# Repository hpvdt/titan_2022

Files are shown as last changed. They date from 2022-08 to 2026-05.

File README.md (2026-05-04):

# TITAN Video System

This is the code and hardware that is used to drive the electronics aboard TITAN for the "drive-by-video" system used for the World Human Powered Speed Challenge 2022.

>[!NOTE]
> This repository is meant to a snapshot of the system used for the 2022 system for TITAN, and was archived in November 2023. It was only unarchived to add a written summary of [operating instructions](./OPERATION.md) should it need to be reused. However no changes to the system itself have happened since 2023.
>
> For information on the the newest system in 2026 please go to that one's [separate repository](https://github.com/savob/titan_2026).

This code is spread across two types of devices, an STM32 microcontroller (STM32F103C8 is used in current models) and Raspberry Pis (RPi) Model 3B+'s. Each rider has an RPi for a total of two units, while there is only one STM32 for the vehicle. The STM32 is primarily responsible for collecting vehicle data and passing it to the RPis when requested. The RPis are responsible for displaying the video feed from the RPi Cameras used (hence why each rider needs their own) with an overlay of data collected inside the vehicle. This overlay is tailored to each rider.

There is an additional redundant video system for the front rider based on analog video to minimize potential failure points. This system was entirely off the shelf except for the power regulator, and was entirely disconnected from the remainder of TITAN's electronics to prevent any failure cascade affecting it.

## Folders

The repository is split into folders based on function.

Folder | Purpose
------ | -------
`Hardware` | Hardware files for our circuit boards
`Microcontroller Code` | STM32 Code
`vision` | RPi video code in C

## Hardware

The hardware for TITAN was all designed in [KiCad](https://www.kicad.org/) there are all three boards designed for TITAN with a `readme.md` explaining their purposes. Below is a block diagram of the TITAN system.

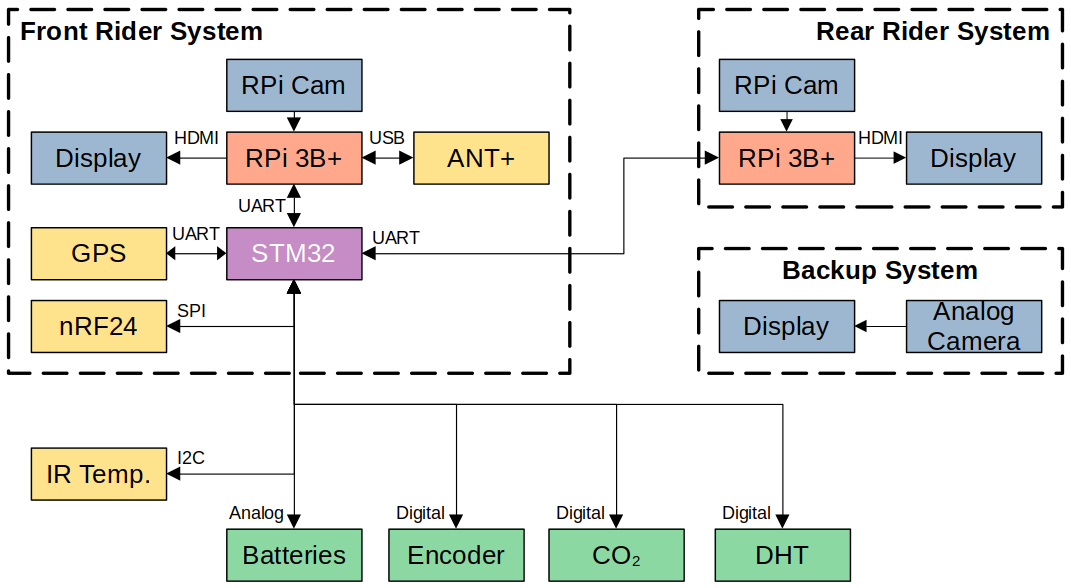
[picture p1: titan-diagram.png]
TITAN Block Diagram


## Microcontroller Code

This is the collection of code prepared for the microcontroller on TITAN. It contains the unit tests we prepared when developing and testing different features that would eventually be integrated into TITAN, a local copy of the GPS library we use, and the overall program for TITAN.

TITAN was initially coded entirely within the Arduino IDE, however we migrated to using VS Code and PlatformIO to help make development easier and also make use of debugging features absent in the original Arduino IDE.

## Raspberry Pi Code

These are responsible for putting video on the displays for the riders to see, overlaid with information about TITAN. One of the RPi's has an ANT+ USB module used to collect data from the heart rate monitor and power pedals each rider has and feed it to the STM32 to pass onto the other RPi.

**The program for running the video feed is run as a separate process to the overlay**, this way if there is a hardware malfunction for the overlay (e.g. the STM32 freezes) then the video feed is uninterrupted for the riders.

The code for vision is split between Python and C. The video related code is written in Python, as well as a few other scripts for operation. The overlay code is written in C using the chipset driver library unique to the RPi 3 hardware to draw the overlay so it cannot be used on RPi models other then the 3B or 3B+ (and must be compiled specifically for each model).

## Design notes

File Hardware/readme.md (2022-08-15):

# TITAN Hardware

These folders contain the files related to hardware designed to operate TITAN. They were all designed using KiCad 6.0.2.

## Overview

The TITAN hardware is designed to primarily be a HAT (**HA**rdware on **T**op) for the Raspberry Pi 3B+s we use for video. This form factor was chosen to reduce the overall footprint of the system compared to the original 2019 system which used a ribbon cable between the RPi and boards. This also reduces the chance of incorrect connections since the HAT can only be seated one way. At the heart of the HAT, there is an STM32F103C microcontroller which communicates with the RPis and various sensors around TITAN via the various connections present.

These HATs perform 4 main functions:
1. Regulate power for their RPi and monitor from the battery. (Reverse polarity and undervoltage protection built in).
2. Facilitate communication between RPis via an STM32 microcontroller
3. Collect data from TITAN using the STM32 microcontroller
4. Handle telemetry with the chase vechicle

**Functions 2 to 4 are only performed on the "main" (front) unit, where the STM32 is.** The secondary (rear) does not have the STM32 mounted and just uses the power system and a header to connect to the main board for data.

## The Boards

There are three boards/folders/projects present in the folder, representing two revisions of the hardware. 

### TITAN Redux (2020)

Following feedback from the 2019 WHPSC and experience in developing [Blueshift](https://github.com/hpvdt/blueshift), an initial revision of TITAN was made in the fall of 2020, dubbed `titan_redux`. This was the main revision from the 2019 system, moving to the HAT form factor which worked on Blueshift as well as moving to embed the microconroller directly on the board (as opposed to seating a "Blue Pill" development board) and using SMT to reduce the overall size.

This was largely successful and allowed most of the code that went into TITAN in 2022 to be properly tested. There were only two notable issues with it:
1. The RX and TX lines for the GPS were not properly crossed over to the STM32.
2. The 5V regulator was removed for undocumented reasons, likely due to a failure.

### TITAN 2022

The more straightforwardly named `titan_2022` is a revision of the Redux board. It addresses the issues it had as well as adding support for new features while maintaining the same RPi HAT form. A brief of the changes:

- Fixed UART lines
- Rearranged board for improved button access
- Rearranged sensors to simplify routing
- Changed to a different 5V regulator (largely due to supply issues)
- Moved DHT sensor and encoder comparator off-board
- Added headers for monitoring CO2 and brake temperature

### TITAN Wheel (2022)

As part of the revision process from redux to the 2022 system a daughter board to collect wheel data was prepared called `titan_wheel`. This board houses the brake temperature sensor as well as the optical encoder and its conditioning circuitry. It was designed to fit within the wheel structure close to the brake disk.

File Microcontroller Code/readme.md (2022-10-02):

# Microcontroller Code

There are three folders here related to the code for the STM32 used in TITAN. Some parts written for the Arduino IDE, some for PlatformIO in VS Code.

Folder | Purpose
------ | -------
`Microcontroller Unit Tests` | Collection of unit tests for different features
`TinyGPS-13` | Local copy of Mikal Hart's [TinyGPS](https://github.com/mikalhart/TinyGPS) library
`titan` | The complete code run in TITAN

## Unit Tests

This is just a bunch of Arduino sketches for us to test out different features of TITAN independantly prior to integration with the main code. 

These tests served to verify that the code would act as needed without any other parts of the code making it act unexpectedly or slowing down coimpilation time during these tests. The unit tests also allowed us to verify and tune the related hardware as needed as was the case for the telemetry features and optical encoder for wheel speed/distance.

## TinyGPS

Just a local copy of the TinyGPS library. Largely kept from the previous collection microcontroller code.

## TITAN STM32 Code

All code for the STM32 is written in C/C++ using the PlatformIO addon for VS Code. It primarily collects data and providing it on request over a serial (UART) line to the connected RPis. It also has telemetry capabilities using an nRF24L01 module and GPS capabilities using an "Ultimate GPS Module" (MTK3339). Data collected by the STM32:

* Optical encoder for wheel
  * Speed
  * Distance travelled
* Temperature and humidity of external air using a DHT22 module
* Battery levels
* GPS data using MTK3339 module
  * Position coordinates
  * Speed (as a backup to encoder)
* Biometric information for riders supplied by RPi with ANT+ module *(explained later)*
  * Heart rate (BPM)
  * Power output (W)
  * Cadence (RPM)
* Brake disk temperatures using MLX90614 sensors
* Internal CO2 levels from an MH-Z19C sensor

In addition to this data collected directly by itself, it also acts as a messenger to pass ANT+ data between the RPis. For each of our two riders the following data is provided to the STM32:

* Cadence
* Heart rate
* Instantanious power

*Note on the communication:* the data was all initially communicated in plaintext as seperate queries (e.g. `s` for speed from the RPi, and the STM32 would respond with `$123.3`). This was found to be increadibly slow and error prone, so we've move to more condensed, binary encoded data exchanges to speed up communication between the RPis, telemetry, and STM32.

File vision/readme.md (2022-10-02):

# RPi Vision Code

This folder is the collection of vision system code running on the RPis. Split between C and Python code.

## Operation

The RPis are configured to boot this system automatically when powered by executing the `titan_startup.py` script when booted (done by editing [rc.local](https://linuxhint.com/use-etc-rc-local-boot/)). To speed this process up, the RPis are configured to boot to command line (CLI) rather than starting the graphical user interface; we believe this also slightly improves the speed of the system.

`titan_startup.py` then launches a series of other processes that collectively represent the TITAN vision system.

* `power_off.py` is launched to watch for a press of the 'OFF' button and react accordingly
* `go_to_desktop.py` watches for a press of the 'ON' button and shuts down the vision system to start the desktop environment (useful for development)
* `camera.py` starts the camera feed and camera recordings

Once these are running, the startup script then responsible for determining whether the RPi is supposed to be the front or rear rider's system based on the presence or absence (respectively) of an ANT+ reciever, and launching the overlay program, `bike.bin`, accordingly by passing it the right arguements. 

* If it is the rear system (no ANT+ modules connected), then the startup script just launches `bike.bin` with the arguments needed for the rear system.
* If it is the front system (ANT+ module present), then the startup script launches the `titanant.py` script to read the ANT+ data and pipe it into `bike.bin` to be overlaid and fed to the STM32.

**NOTE: All these scripts/executables are run as seperate processes so that if one fails, the others should continue unhindered. Namely the video is never interrupted to the riders.**

## Overlay Code

The overlay code is the main product of this folder, and written in C. It is split up across several function specific C files. Handles communication with the STM32 for data, overlay drawing, and logging as requested.

* `main` - Main file. Reads in arguements provided to determine behaviour (e.g. 'front' or 'rear' system, record logs or not) and then run the main loop to create overlays.
* `antInterface` - Used to process the piped in ANT data from `titanant.py` for use on the overlays and passing on the the STM32
* `overlay` - Responsible for the actually drawing of the overlay. Uses the chipset driver library unique to the RPi 3 hardware to draw the overlay over the video feed. This limits its use to only the 3B or 3B+, and `bike.bin` must be compiled specifically for each model.
* `logging` - Used to write a CSV file of all data collected on the bike
* `racesim` - A C version of our Race Simulation file used to determine how our bike should perform and then compare to how it actually is to see if we're exceeding expectations or not. **UNTESTED**.
* `serialComs` - Responsible for handling communication with the STM32
* `timeTrial` - Used to monitor timing of the code to see how long different sections take to execute. *Used for development purposes, not needed for the riders.*

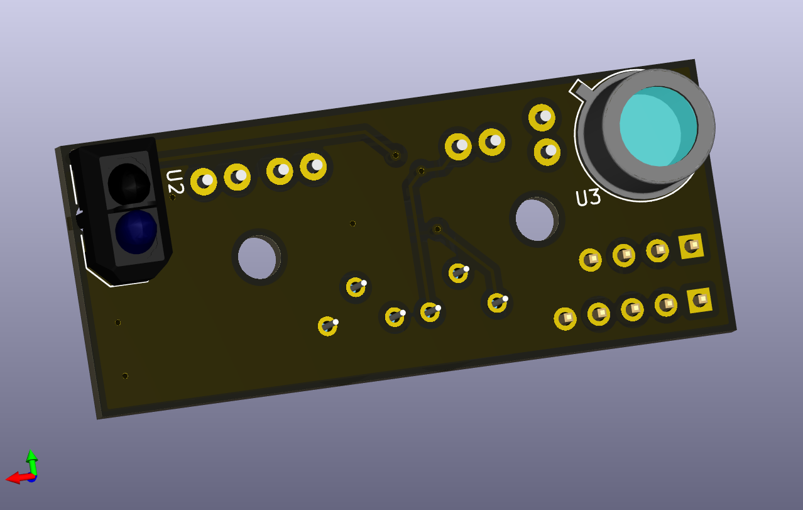
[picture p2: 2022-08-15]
Hardware/titan_wheel/titan_wheel_bottom.png

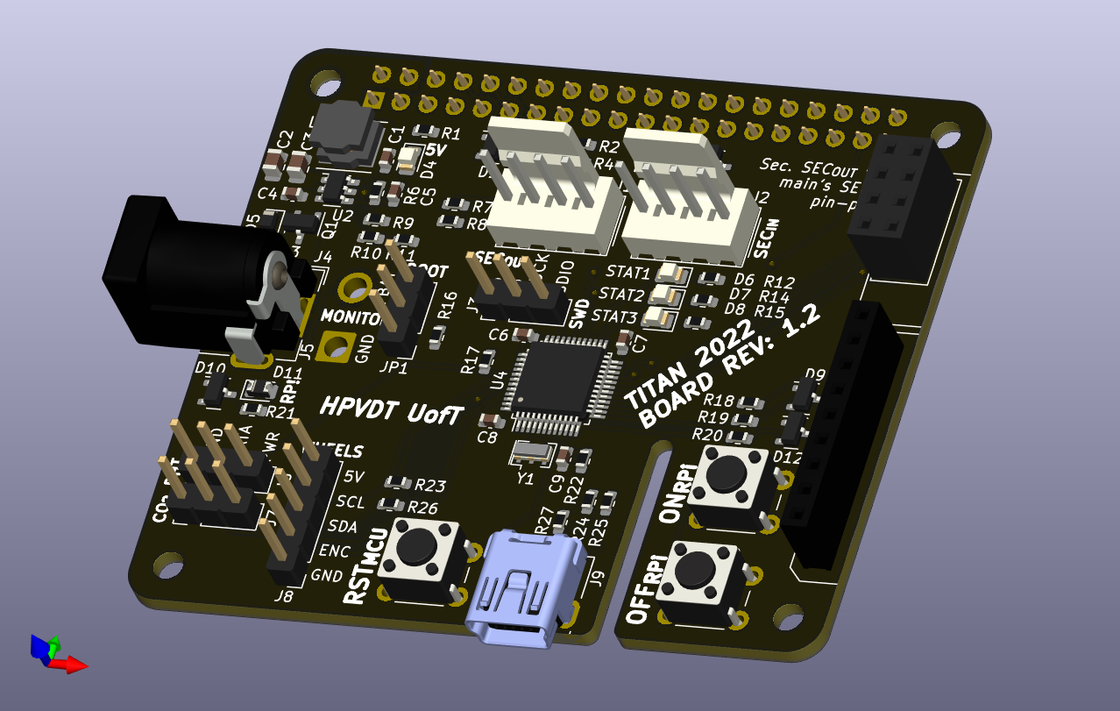
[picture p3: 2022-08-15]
Hardware/titan_2022/titan_2022_top.png

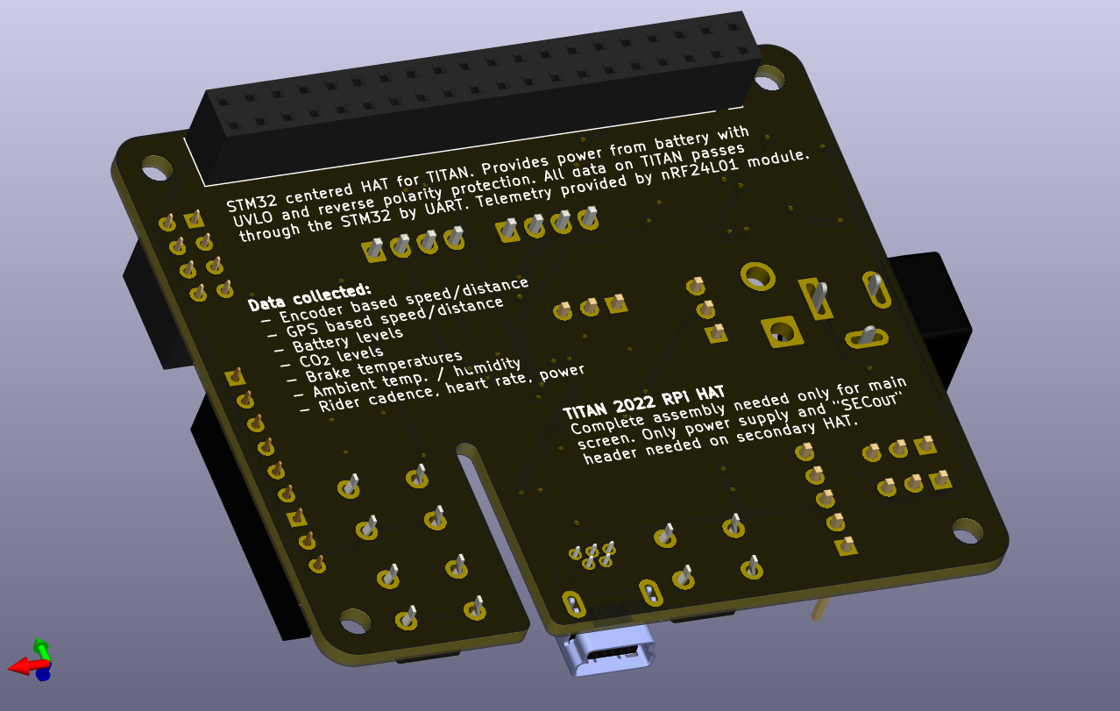
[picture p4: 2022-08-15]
Hardware/titan_2022/titan_2022_bottom.png

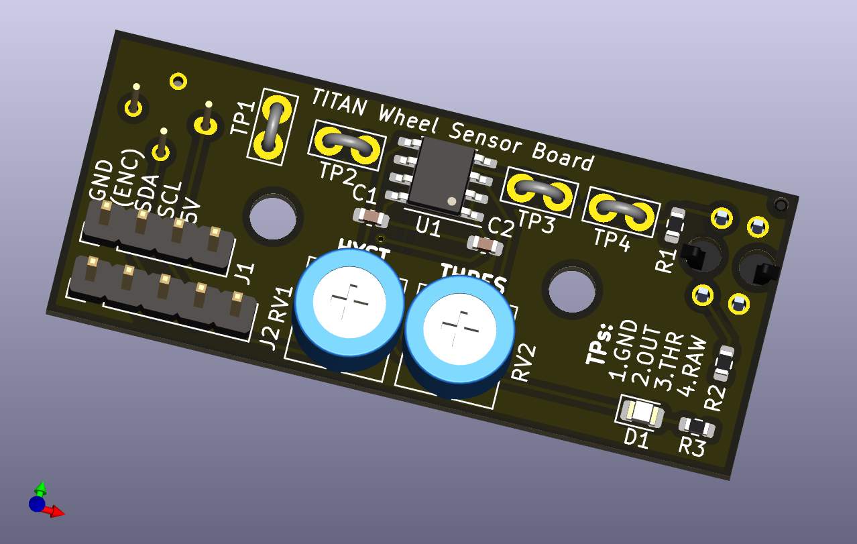
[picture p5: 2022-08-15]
Hardware/titan_wheel/titan_wheel_top.png

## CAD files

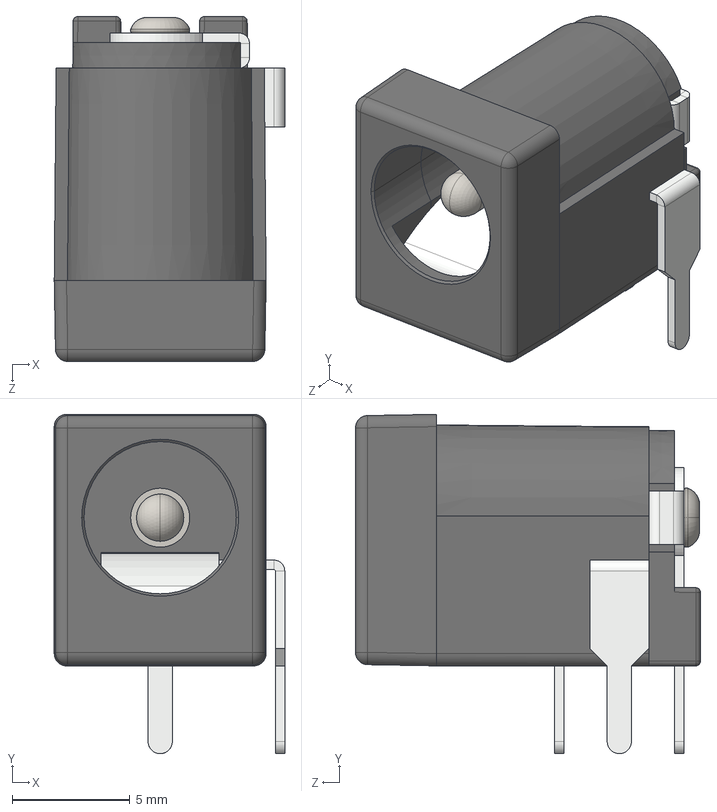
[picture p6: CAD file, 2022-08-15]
Hardware/titan_2022/DC Power Jack 5.5mm x 2.1mm.STEP
9.77 x 14.4 x 14.6 mm

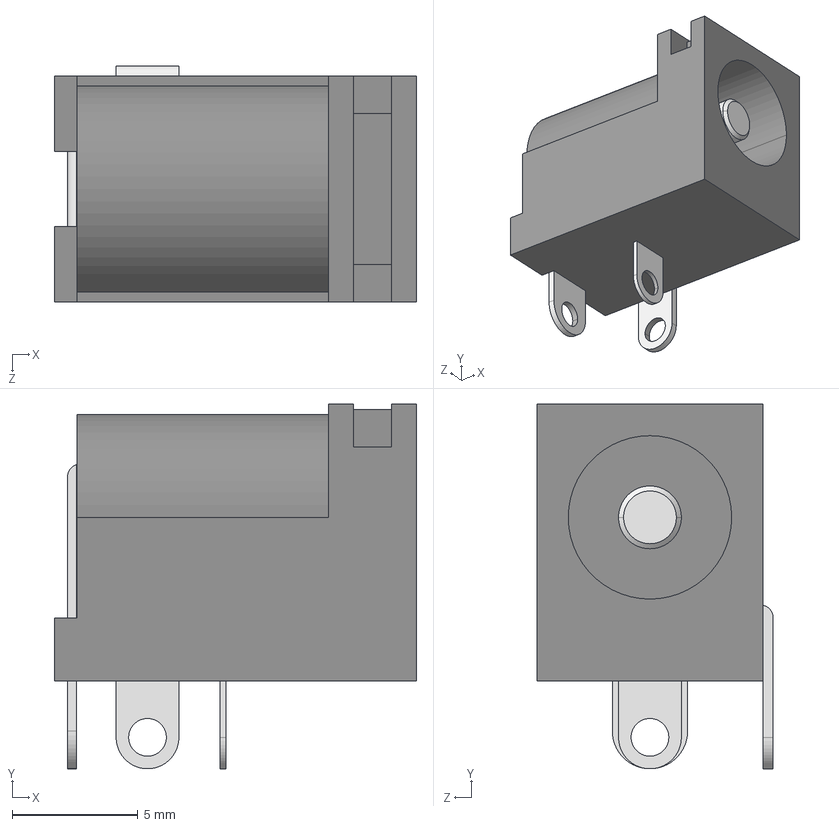
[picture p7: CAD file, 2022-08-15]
Hardware/titan_redux/CUI_DEVICES_PJ-002B.step
14.4 x 14.5 x 9.40 mm

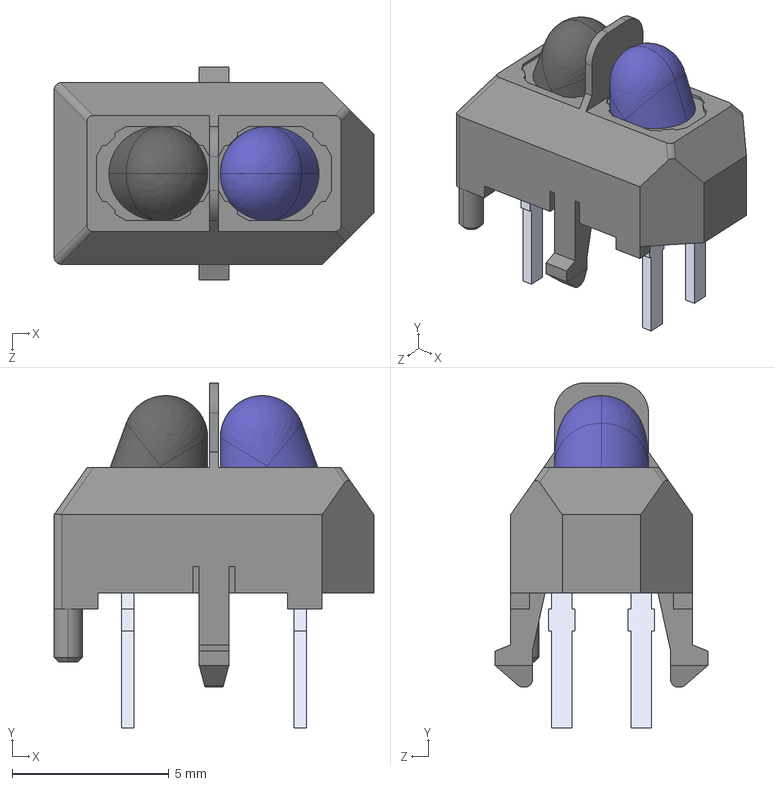
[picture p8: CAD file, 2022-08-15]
Hardware/titan_wheel/TCRT5000/TCRT5000.step
10.2 x 11.0 x 6.80 mm

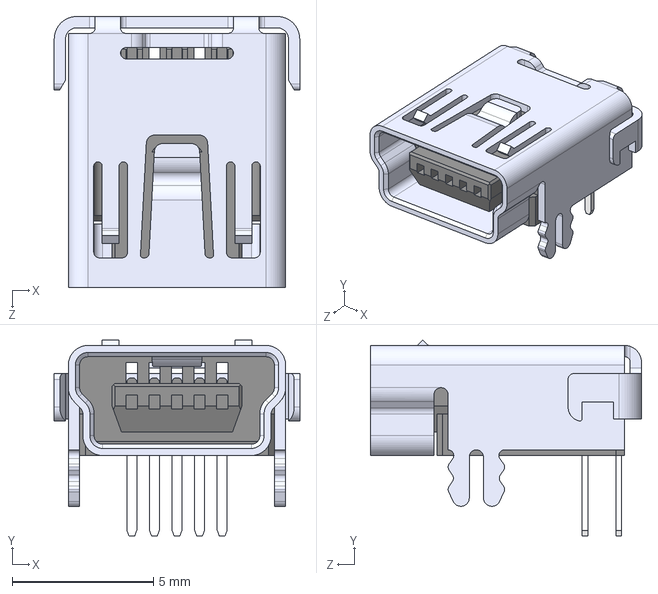
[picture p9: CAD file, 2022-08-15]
Hardware/titan_2022/2172034-1/2172034-1--3DModel-STEP-56544.STEP
8.70 x 6.94 x 9.60 mm

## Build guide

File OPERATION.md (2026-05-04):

# Setup and Operating Instructions

TITAN was designed and tested to be a pretty simple system to operate by requiring no user input beyond a the input to power on, once assembled correctly.

## Batteries and Power

_The system's life force!_

The batteries TITAN 2022 was **designed for are 3S LiFePO4 batteries**, as such their working range of voltages are generally 9.0&nbsp;V to 10.8&nbsp;V with their nominal voltage being 9.9&nbsp;V. Prior to operation they should be charged fully.

The exact power draw of TITAN is approximately 10&nbsp;W per RPi vision system, about half that for the analog back up system. As such a 1000&nbsp;mAh 3S LiFePO4 battery can supply a vision system for an hour of operation is is plenty for most of our 20 minute heats - but warrants changes for longer testing sessions.

## Assembly/Setup

TITAN was once, assembled, now it likely is no longer, so someone's got to put it back together. This will be written assuming TITAN's basically being entirely rebuilt.

### Lists of Parts

>[!NOTE]
> These lists do not account for any spare parts, those are up to your discretion.

There are a fair few parts to TITAN needed for operation that need to be packed listed below. Only one unit is needed of each unless specified otherwise.

- 2 x Raspberry Pis Model 3A+ or 3B+
- 2 x 16 GB micro SD cards (larger is fine but will not be used)
- 2 x approximately 10" 720p HDMI display, 12&nbsp;V supply
- 2 x Raspberry Pi "Spy" camera
- TITAN 2022 HAT assembled for primary operation (microcontroller present and more connectors)
- TITAN 2022 HAT assembled for secondary operation
- HDMI cable, 30&nbsp;cm long
- "Ultimate" GPS module
- GPS antenna with SMA connector on 3&nbsp;m cable
- nRF24L01+PA+LNA radio module
- 2.4 GHz antenna with 3&nbsp;m cable
- ANT+ reciever (USB-A)
- Analog pin hole video camera, 12&nbsp;V supply
- 7" analog input display, 12&nbsp;V supply

The following are needed but will likely be already integrated into TITAN's structure, so they don't need to be "packed".

- 3 x Battery extension leads, T connector to barrel jack, 1.5&nbsp;m long
- 2 x 5.5&nbsp;mm barrel jack to barrel jack cable, 3&nbsp;m long
- Rear wheel sensor board with harness soldered on
- Brake disk temperature sensor for front wheel with USB-A connector
- USB-A to USB-A cable, 3&nbsp;m long
- HDMI cable, 3&nbsp;m long
- MH-Z19 CO2 sensor with 3&nbsp;m long cable
- DHT22 sensor with 3&nbsp;m long cable
- 12&nbsp;V power distribution board
- RCA coax video cable, 3&nbsp;m long

### Setup Procedure

>[!CAUTION]
> **All systems must be entirely unpowered for setup!** Remove any and all batteries. The system was not designed for hot-plugging any component so damage may occur as a result.

This starts with the primary digital vision systems for each rider, then the backup system provided to the primary rider.

>[!TIP]
> These steps may be performed in any order. Here they are presented in the order that will likely be the most convenient to perform.

1. Check the sensors are installed
   - Front wheel brake temperature sensor in wheel bracket
   - Wheel sensor board in the rear wheel's bracket
   - DHT22 near the air inlet
   - MH-Z19 sensor between the heads of riders
2. Check that the auxiliary sensor connections are made
   - Front wheel sensor intermediate connector is mated near front yoke (might have been disconnected during maintenance or removal of yoke)
   - Front wheel to rear wheel cable harness connection
   - Camera cable extenders are properly securing the ribbon cables if used
   - Antenna cables are routed to electronics area
3. Image the micro SD cards for each RPi and insert them into the RPis
4. Connect the camera cables to each RPi, ensuring they are installed correctly by being perfectly normal to the board
5. Install the RPi HATs, mounted with threaded plastic spacer ideally
6. Insert the ANT+ receiver into the primary/front rider's RPi
7. Connect the sensor to the primary system's hat, all connectors will only fit where they are meant to
8. Connect the monitors to the RPis using HDMI cables for video and provide them power from same RPi's HAT
   - In TITAN there should be wires routed from the electronics area to the front rider's viewing area
   - Even the rear rider may require some extension cables to better position the electronics
9. Connect the RPi HATs with the bridge cable, from `SEC_OUT` on the secondary (rear rider's) HAT to `SEC_IN` on the primary HAT
10. Connect the backup camera to the backup monitor using an RCA cable
11. Connect the backup camera and screen to the 12&nbsp;V power board

## Start Up

With TITAN assembled correctly the process to launch the system is pretty straight forward.

> [!CAUTION]
> Failure to follow the battery connection sequence properly may damage the hardware.

1. Ensure batteries are fully charged
2. Plug in the batteries following this exact order. Each system should automatically begin booting when their battery is connected
   1. Primary (front) system
   2. Secondary (rear) system
   3. Backup system
3. Press the on button (`ON_RPi`) on RPi systems to boot them if needed - for example if they were shutdown without battery removal

The backup system should show the video feed immediately when turned on. The RPi systems will take about 30 seconds to put the video on screen, which will be preceded with boot messages and a printing of the system's configuration.

## Shut Down

Whenever power is going to be removed from TITAN the following procedure should be followed. Be it at the end of a run, or to conserve battery when staging before a run.

> [!CAUTION]
> Failure to follow this properly may damage the hardware or risk corrupting the data on the RPis.

1. Press the off button (`OFF_RPi`) on the HAT
2. Wait for the video feed to go off and the RPi to shut down properly
   - The video feed should disappear within seconds after the button is pressed, if not press the button again
   - Repeated presses of the off button will not adversely affect the system
   - If the system doesn't shutdown within a minute you may need to connect a keyboard or simply pull the power risking data loss
   - As the RPi shuts down its status LED will flash ten times at 2&nbsp;Hz before going out, that signals it is safe to remove power
3. If desired, disconnect the batteries. They **MUST** be removed in the reverse order they were installed in:
   1. Backup display
   2. Secondary system
   3. Primary system

If the batteries are left in place, the RPis can be turned on at the press of the on button (`ON_RPi`). This is useful to do for staging before a run. There is no required order to follow when turning on RPis in this manner because the power supplies have all stabilized.

## Transferring Data To or From the RPis

My _(Savo's)_ preferred method to transfer data was to remove the RPi's micro SD card _(after a proper shutdown with battery removal!)_ and insert it into my computer and directly copy the data of interest onto the computer that way. The only issue is that you'll likely need a Linux machine to recognize the file system the RPi's use. Having the SD card in my computer also made it easy to edit some of the scripts to handle things like new power pedals.

Other options include network access or using the RPi's as a normal desktop and a USB drive to ferry the data to another computer.

>[!IMPORTANT]
> To get to the desktop of a TITAN RPi one can press the RPi's on button (`ON_RPi`) during operation of the vision system to stop the vision system.

If the button is not working, one can try to manually enter the following sequence of command blindly into the terminal with a keyboard to shut the vision system down. _Best of luck console cowboy!_

```bash
sudo pkill bike
sudo pkill python
```

>[!TIP]
> Entering `startx` in the terminal will start the graphical interface if desired for easier operation of the RPis. _Brace yourself for a slow computer experience._

### Log Files and Locations

By default the TITAN system records data in two locations, one for the videos and another for the ride data.

> [!NOTE]
> All recorded files are timestamped in their names with the start of the run. However the **RPis do not keep time when they are off, so these times will likely lag behind the true start time**. To minimize this time discrepancy the RPis should be allowed to connect to the internet to synchronize their clocks regularly.

| Data | Location | Format |
| --- | --- | --- |
| Ride data | `/home/pi/Desktop/vision/bikelogs/` | `.csv` |
| Video recordings | `/home/pi/Videos` | `.h264` |

### Video Conversion

To convert from `.h264` recordings to the more commonly accepted `.mp4` one may use the following `ffmpeg` command with the appropriate file names substituted for "video":

```bash
ffmpeg -r 60 -i video.h264 -c:v copy video.mp4
```

>[!NOTE]
> The video recordings are known to have portions where the video seems to skip ahead for split seconds. This is likely due to the recording program getting overwhelmed or some hiccup in the `.mp4` conversion process.
>
> Furthermore, the video and overlay/logging are run as separate process so their staring time stamps will likely differ and need a little effort to align.

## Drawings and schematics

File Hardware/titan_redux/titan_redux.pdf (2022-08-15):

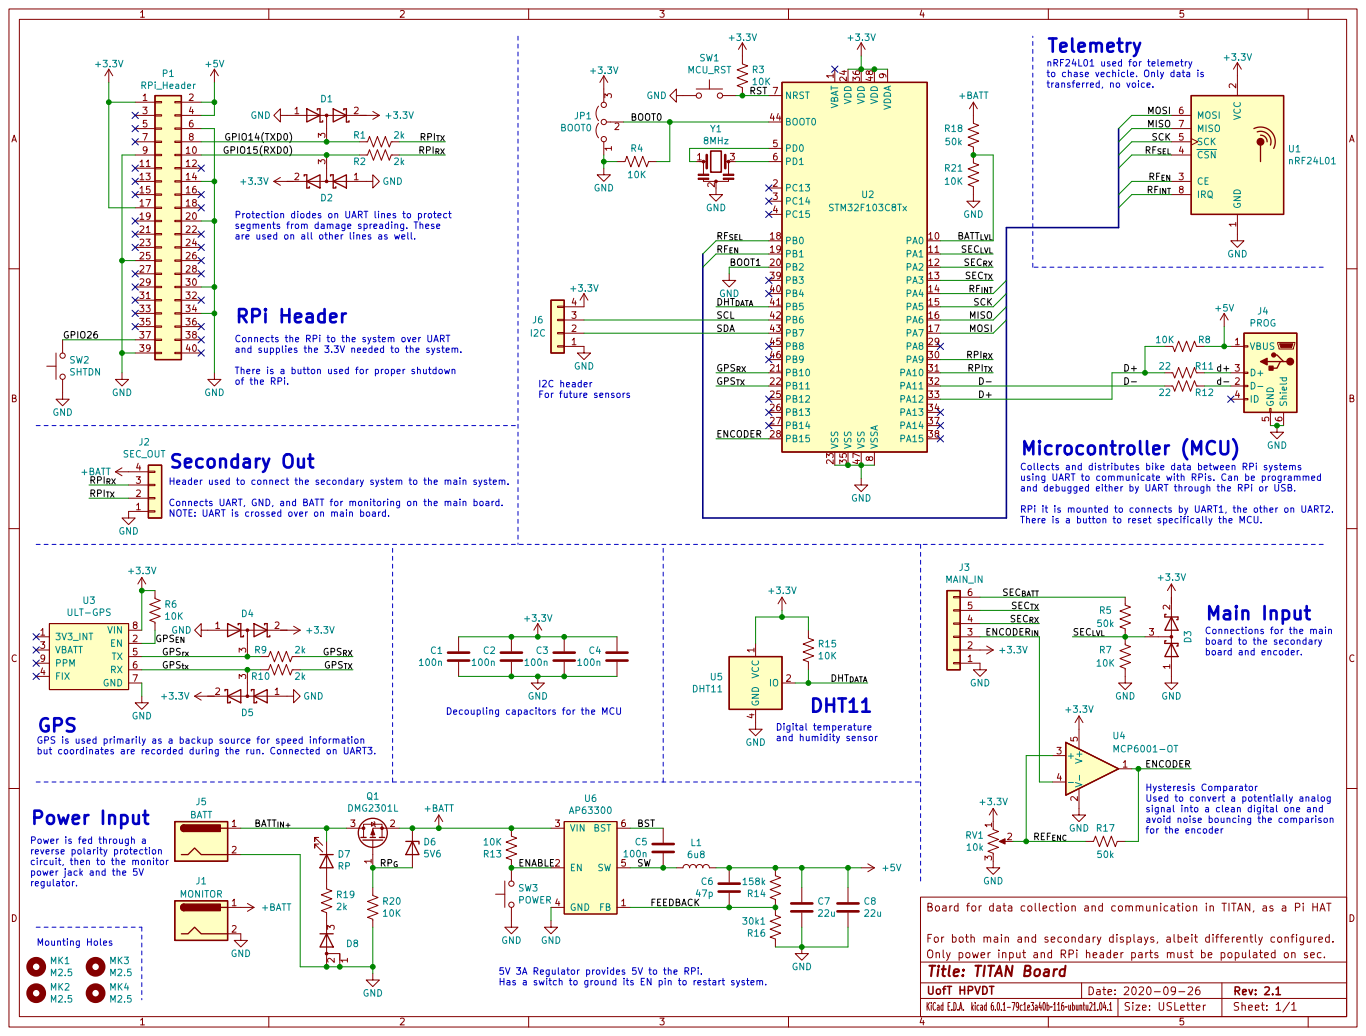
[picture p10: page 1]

transferred, no voice. Telemetry

+3.3VGND

1 PA0 10 PA1 11 PA2 12 PA3 13 PA4 14 PA5 15 PA6 16 PA7 17 PB0 18 PB1 19 PC13 2 PB2 20 PB10 21 PB11 22 VSS 23 VDD 24 PB12 25 PB13 26 PB14 27 PB15 28 PA8 29 PC14 3 PA9 30 PA10 31 PA11 32 PA12 33 PA13 34 VSS 35 VDD 36 PA14 37 PA15 38 PB3 39 PC15 4 PB4 40 PB5 41 PB6 42 PB7 43 BOOT0 44 PB8 45 PB9 46 VSS 47 VDD 48 PD0 5 PD1 6 NRST 7 VSSA

to chase vechicle. Only data is

2 CE 3 ~{CSN} 4 SCK 5 MOSI 6 MISO 7

Protection diodes on UART lines to protect
segments from damage spreading. These

are used on all other lines as well. GPS

Connects the RPi to the system over UART
and supplies the 3.3V needed to the system.

There is a button used for proper shutdown

board to the secondary board and encoder. Microcontroller (MCU)

Collects and distributes bike data between RPi systems
using UART to communicate with RPis. Can be programmed
and debugged either by UART through the RPi or USB.

Connects UART, GND, and BATT for monitoring on the main board. NOTE: UART is crossed over on main board. Mounting Holes

RPi it is mounted to connects by UART1, the other on UART2.
There is a button to reset specifically the MCU.

for the encoder Digital temperature
and humidity sensor

GPS is used primarily as a backup source for speed information
but coordinates are recorded during the run. Connected on UART3.

Hysteresis Comparator
Used to convert a potentially analog
signal into a clean digital one and
avoid noise bouncing the comparison

Power is fed through a
reverse polarity protection
circuit, then to the monitor power jack and the 5V

Board for data collection and communication in TITAN, as a Pi HAT KiCad E.D.A. kicad 6.0.1-79c1e3a40b~116~ubuntu21.04.1
For both main and secondary displays, albeit differently configured.
UofT HPVDT Only power input and RPi header parts must be populated on sec.

5V 3A Regulator provides 5V to the RPi.
Has a switch to ground its EN pin to restart system.

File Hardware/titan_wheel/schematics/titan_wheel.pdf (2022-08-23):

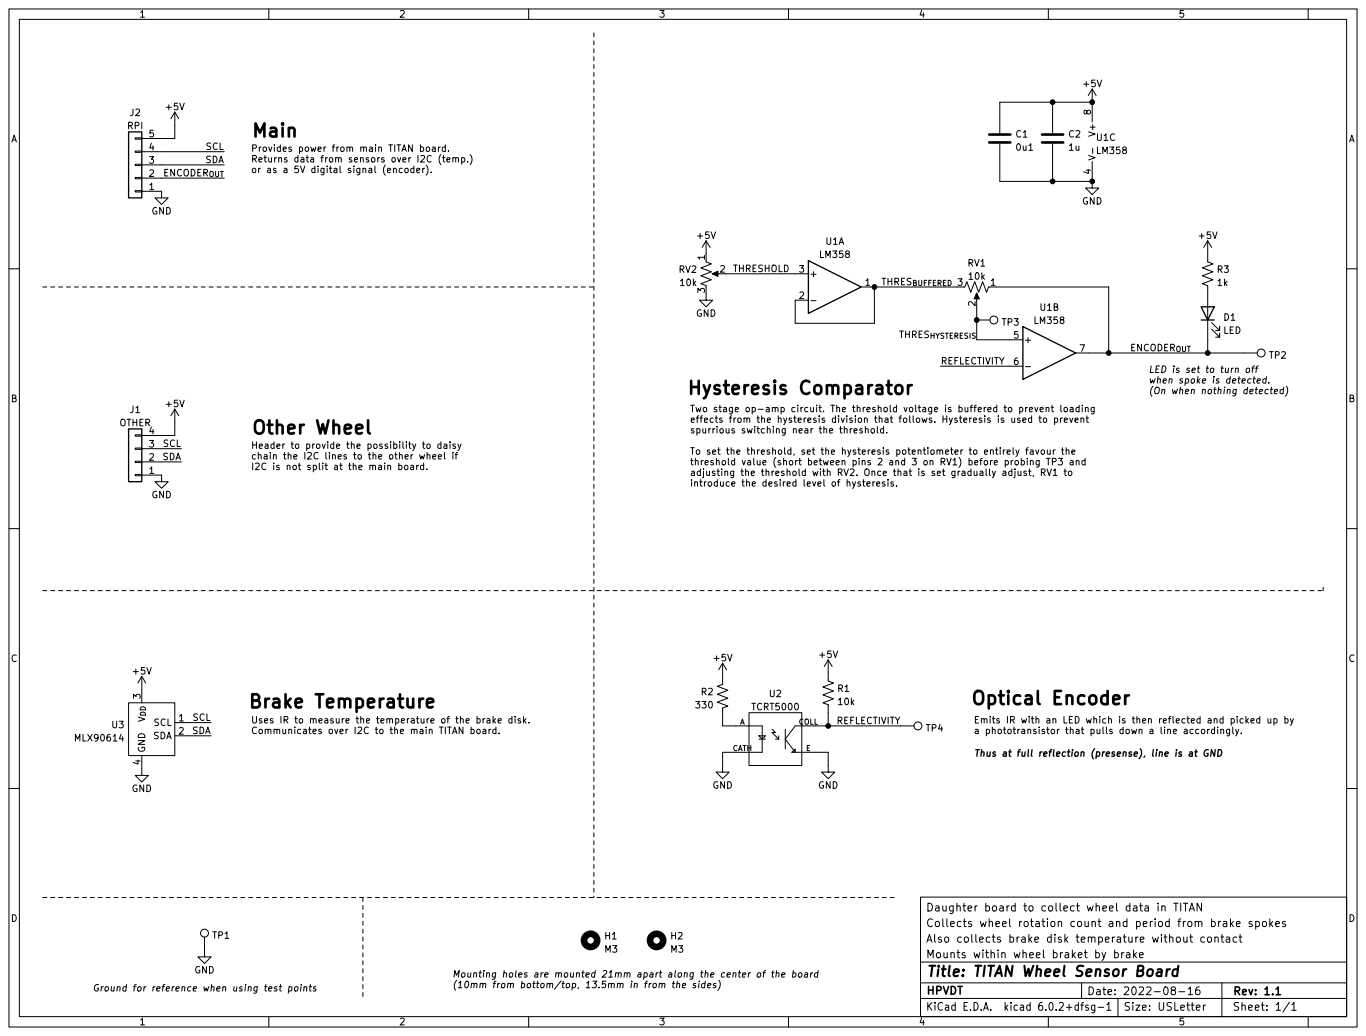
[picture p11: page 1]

Provides power from main TITAN board.
Returns data from sensors over I2C (temp.)
or as a 5V digital signal (encoder).

LED is set to turn off when spoke is detected.

(On when nothing detected)

Two stage op-amp circuit. The threshold voltage is buffered to prevent loading
effects from the hysteresis division that follows. Hysteresis is used to prevent
spurrious switching near the threshold.

Header to provide the possibility to daisy
chain the I2C lines to the other wheel if
I2C is not split at the main board.

To set the threshold, set the hysteresis potentiometer to entirely favour the
threshold value (short between pins 2 and 3 on RV1) before probing TP3 and
adjusting the threshold with RV2. Once that is set gradually adjust, RV1 to
introduce the desired level of hysteresis.

Uses IR to measure the temperature of the brake disk. Communicates over I2C to the main TITAN board. Brake Temperature

Emits IR with an LED which is then reflected and picked up by
a phototransistor that pulls down a line accordingly.

Thus at full reflection (presense), line is at GND

Daughter board to collect wheel data in TITAN
Collects wheel rotation count and period from brake spokes
Also collects brake disk temperature without contact
HPVDT Mounts within wheel braket by brake

Mounting holes are mounted 21mm apart along the center of the board
(10mm from bottom/top, 13.5mm in from the sides)

Ground for reference when using test points

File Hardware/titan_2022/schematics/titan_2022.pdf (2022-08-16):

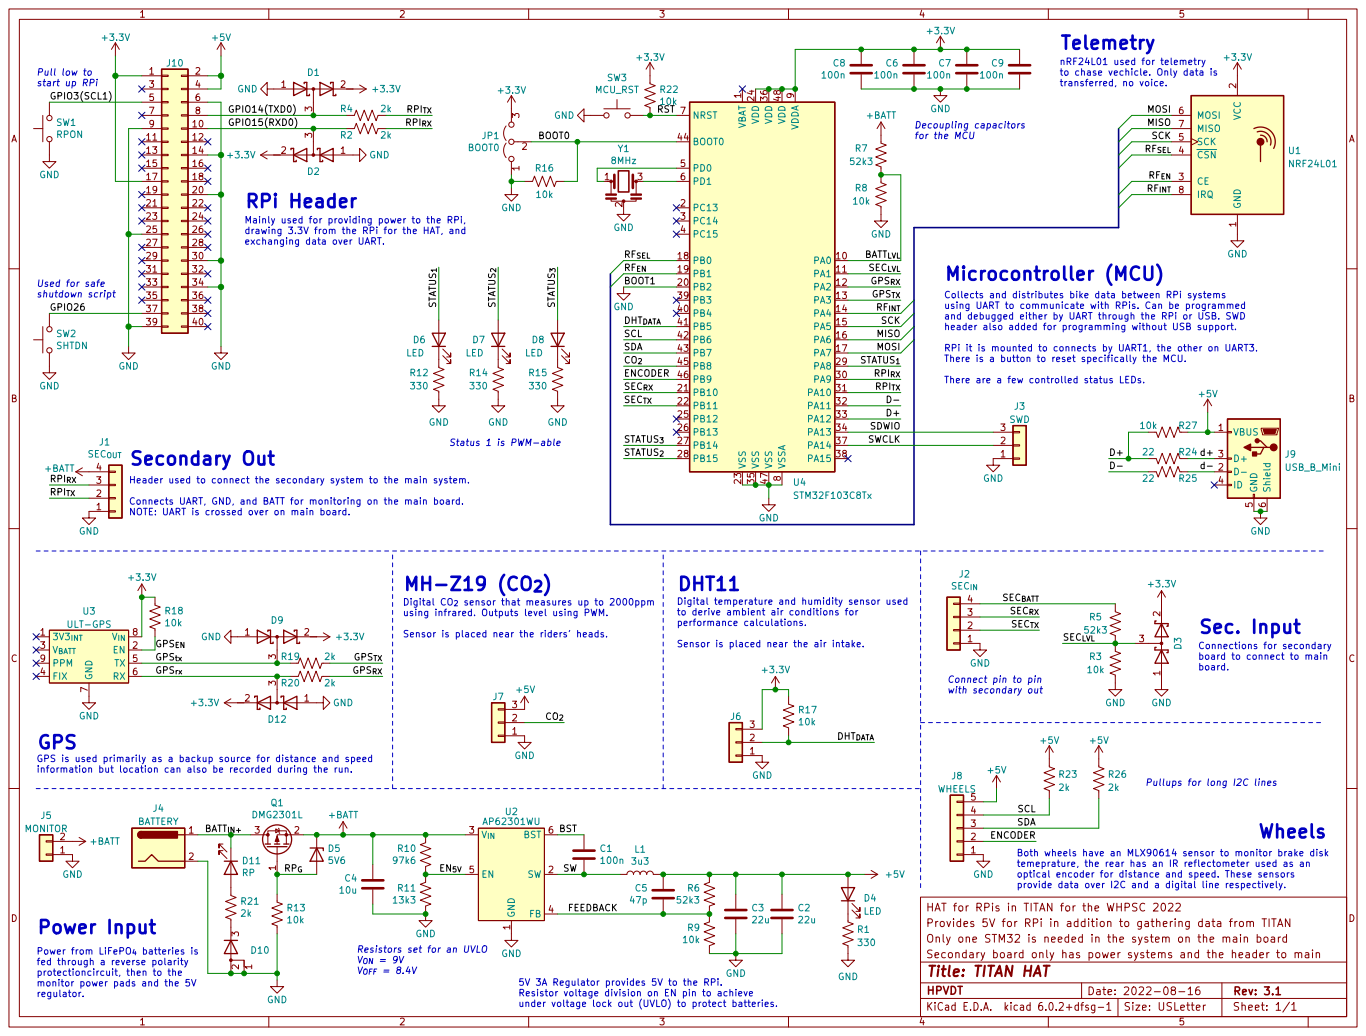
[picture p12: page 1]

transferred, no voice. Telemetry

MH-Z19 (CO_{2}) Status 1 is PWM-able Pull low to
start up RPi

nRF24L01 used for telemetry
to chase vechicle. Only data is

1 PA0 10 PA1 11 PA2 12 PA3 13 PA4 14 PA5 15 PA6 16 PA7 17 PB0 18 PB1 19 PC13 2 PB2 20 PB10 21 PB11 22 VSS 23 VDD 24 PB12 25 PB13 26 PB14 27 PB15 28 PA8 29 PC14 3 PA9 30 PA10 31 PA11 32 PA12 33 PA13 34 VSS 35 VDD 36 PA14 37 PA15 38 PB3 39 PC15 4 PB4 40 PB5 41 PB6 42 PB7 43 BOOT0 44 PB8 45 PB9 46 VSS 47 VDD 48 PD0 5 PD1 6 NRST 7 VSSA
RST

2 CE 3 ~{CSN} 4 SCK 5 MOSI 6 MISO 7

Mainly used for providing power to the RPi,
drawing 3.3V from the RPi for the HAT, and
exchanging data over UART.

Connects UART, GND, and BATT for monitoring on the main board. NOTE: UART is crossed over on main board. Used for safe
shutdown script

Collects and distributes bike data between RPi systems
using UART to communicate with RPis. Can be programmed
and debugged either by UART through the RPi or USB. SWD
header also added for programming without USB support.

RPi it is mounted to connects by UART1, the other on UART3.

There is a button to reset specifically the MCU. There are a few controlled status LEDs. GPS is used primarily as a backup source for distance and speed

Secondary Out
Header used to connect the secondary system to the main system.

DHT11
Digital temperature and humidity sensor used
to derive ambient air conditions for performance calculations.

7 V_{IN} 8 PPM 9 U3 ULT-GPS GND

Digital CO_{2} sensor that measures up to 2000ppm
using infrared. Outputs level using PWM.

Connections for secondary board to connect to main board. GPS

Sensor is placed near the riders' heads.

Sensor is placed near the air intake.

Connect pin to pin
with secondary out

information but location can also be recorded during the run.

Pullups for long I2C lines

1 SW 2 V_{IN} 3 FB 4 EN 5 BST 6 U2 AP62301WU

temeprature, the rear has an IR reflectometer used as an
optical encoder for distance and speed. These sensors
provide data over I2C and a digital line respectively.

HAT for RPis in TITAN for the WHPSC 2022 KiCad E.D.A. kicad 6.0.2+dfsg-1
Provides 5V for RPi in addition to gathering data from TITAN
Only one STM32 is needed in the system on the main board
HPVDT Secondary board only has power systems and the header to main

Power from LiFePO_{4} batteries is
fed through a reverse polarity
protectioncircuit, then to the
monitor power pads and the 5V

Resistors set for an UVLO
V_{OFF} = 8.4V

5V 3A Regulator provides 5V to the RPi.
Resistor voltage division on EN pin to achieve
under voltage lock out (UVLO) to protect batteries.

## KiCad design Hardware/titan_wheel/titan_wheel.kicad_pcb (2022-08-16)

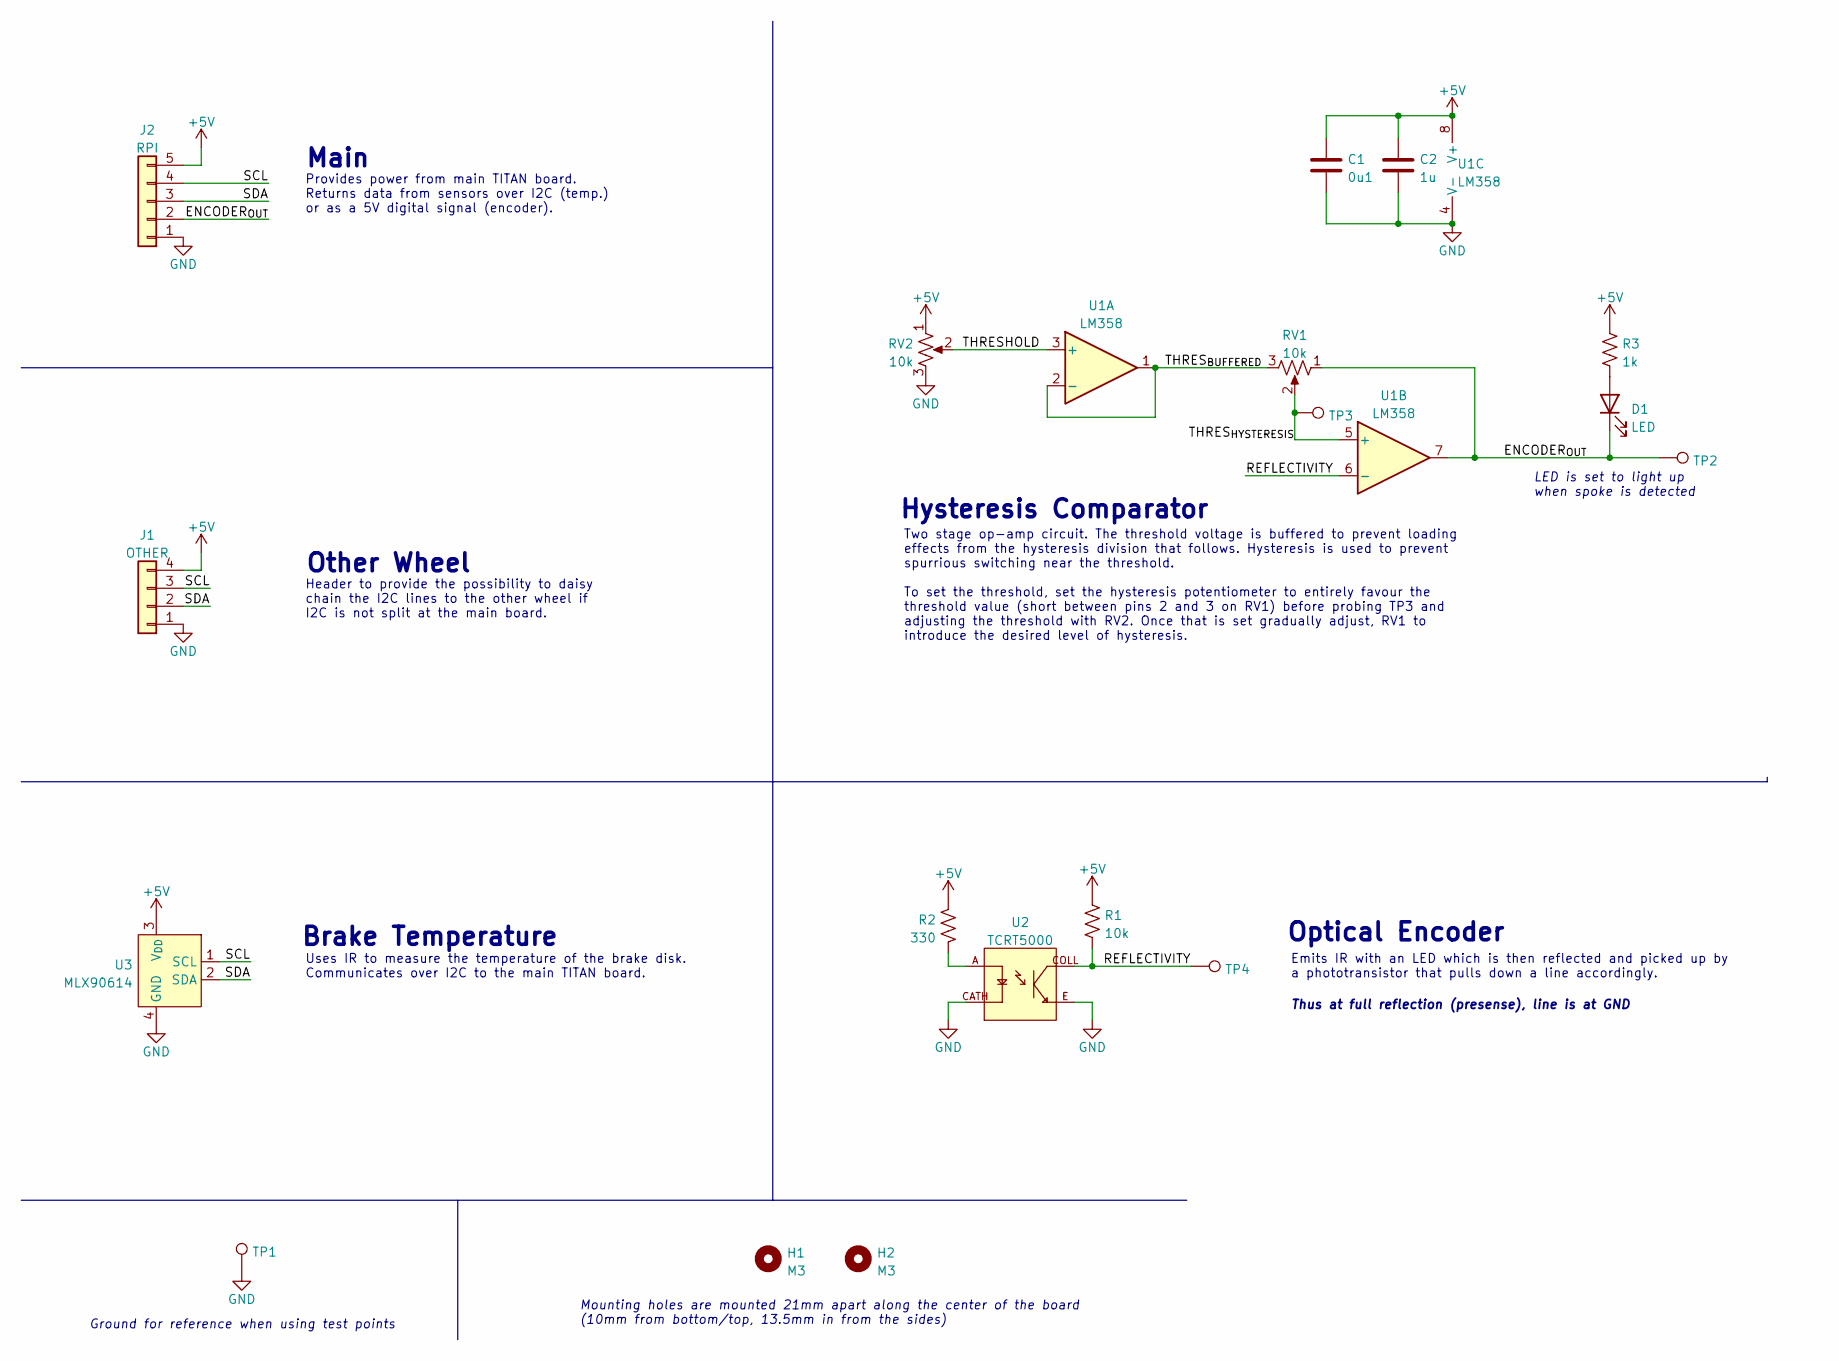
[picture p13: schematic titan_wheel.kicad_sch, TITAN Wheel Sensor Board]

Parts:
C1: 0u1; C_0603_1608Metric
C2: 1u; C_0603_1608Metric
D1: LED; LED_0805_2012Metric
H1, H2: M3; MountingHole_3.2mm_M3
J1: OTHER; PinHeader_1x04_P2.54mm_Vertical
J2: RPI; PinHeader_1x05_P2.54mm_Vertical
R1: 10k; R_0603_1608Metric
R2: 330; R_0603_1608Metric
R3: 1k; R_0603_1608Metric
RV1, RV2: 10k; Potentiometer_Vishay_T73YP_Vertical
TP1, TP2, TP3, TP4: TestPoint; TestPoint_Bridge_Pitch2.54mm_Drill1.0mm
U1: LM358; SOIC-8_3.9x4.9mm_P1.27mm
U2: TCRT5000; OPTO_TCRT5000; PARTREV 1.7
U3: MLX90614; TO-39-4_Window

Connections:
+5V: C1.1, C2.1, J1.4, J2.5, R1.1, R2.2, R3.1, RV2.1, U1.8 (V+), U3.3 (V_{DD})
/ENCODER_{OUT}: D1.1 (K), J2.2, RV1.1, TP2.1, U1.7
/REFLECTIVITY: R1.2, TP4.1, U1.6 (-), U2.COLL
/SCL: J1.3, J2.4, U3.1 (SCL)
/SDA: J1.2, J2.3, U3.2 (SDA)
/THRESHOLD: RV2.2, U1.3 (+)
/THRES_{BUFFERED}: RV1.3, U1.1, U1.2 (-)
/THRES_{HYSTERESIS}: RV1.2, TP3.1, U1.5 (+)
GND: C1.2, C2.2, J1.1, J2.1, RV2.3, TP1.1, U1.4 (V-), U2.CATH, U2.E, U3.4 (GND)
unnamed: D1.2 (A), R3.2
unnamed: R2.1, U2.A

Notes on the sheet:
Mounting holes are mounted 21mm apart along the center of the board (10mm from bottom/top, 13.5mm in from the sides)
Hysteresis Comparator
Provides power from main TITAN board. Returns data from sensors over I2C (temp.) or as a 5V digital signal (encoder).
Emits IR with an LED which is then reflected and picked up by a phototransistor that pulls down a line accordingly.
Two stage op-amp circuit. The threshold voltage is buffered to prevent loading effects from the hysteresis division that follows. Hysteresis is used to prevent spurrious switching near the threshold. To set the threshold, set the hysteresis potentiometer to entirely favour the threshold value (shor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
Ground for reference when using test points
Optical Encoder
Main
Other Wheel
LED is set to light up when spoke is detected
Brake Temperature
Header to provide the possibility to daisy chain the I2C lines to the other wheel if I2C is not split at the main board.
Uses IR to measure the temperature of the brake disk. Communicates over I2C to the main TITAN board.
Thus at full reflection (presense), line is at GND

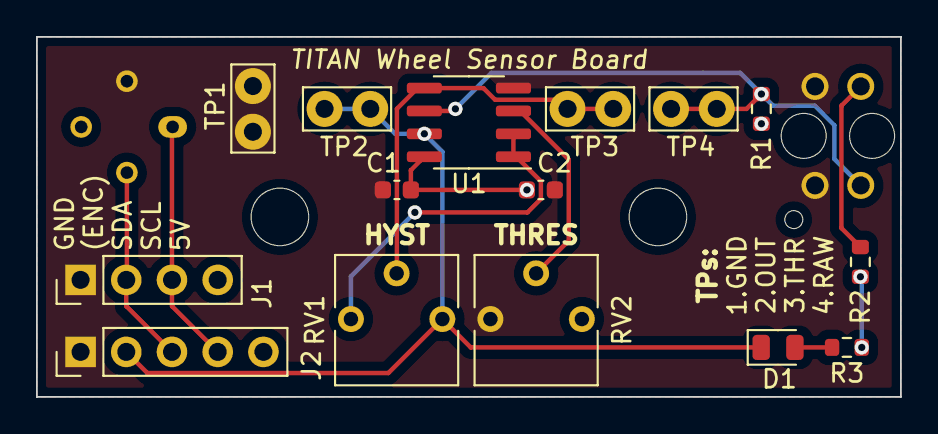
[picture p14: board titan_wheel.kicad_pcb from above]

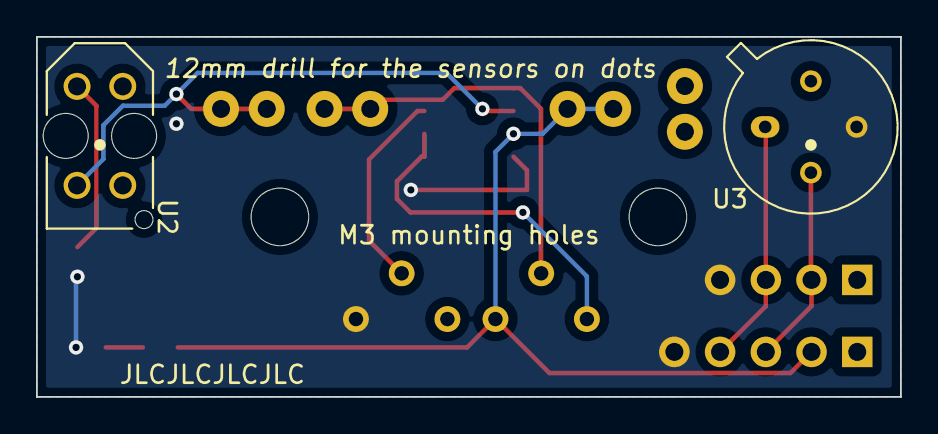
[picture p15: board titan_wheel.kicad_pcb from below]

Board: 2 copper layers, 48.0 x 20.0 mm, 19 parts (2 on the bottom side), 11 nets.

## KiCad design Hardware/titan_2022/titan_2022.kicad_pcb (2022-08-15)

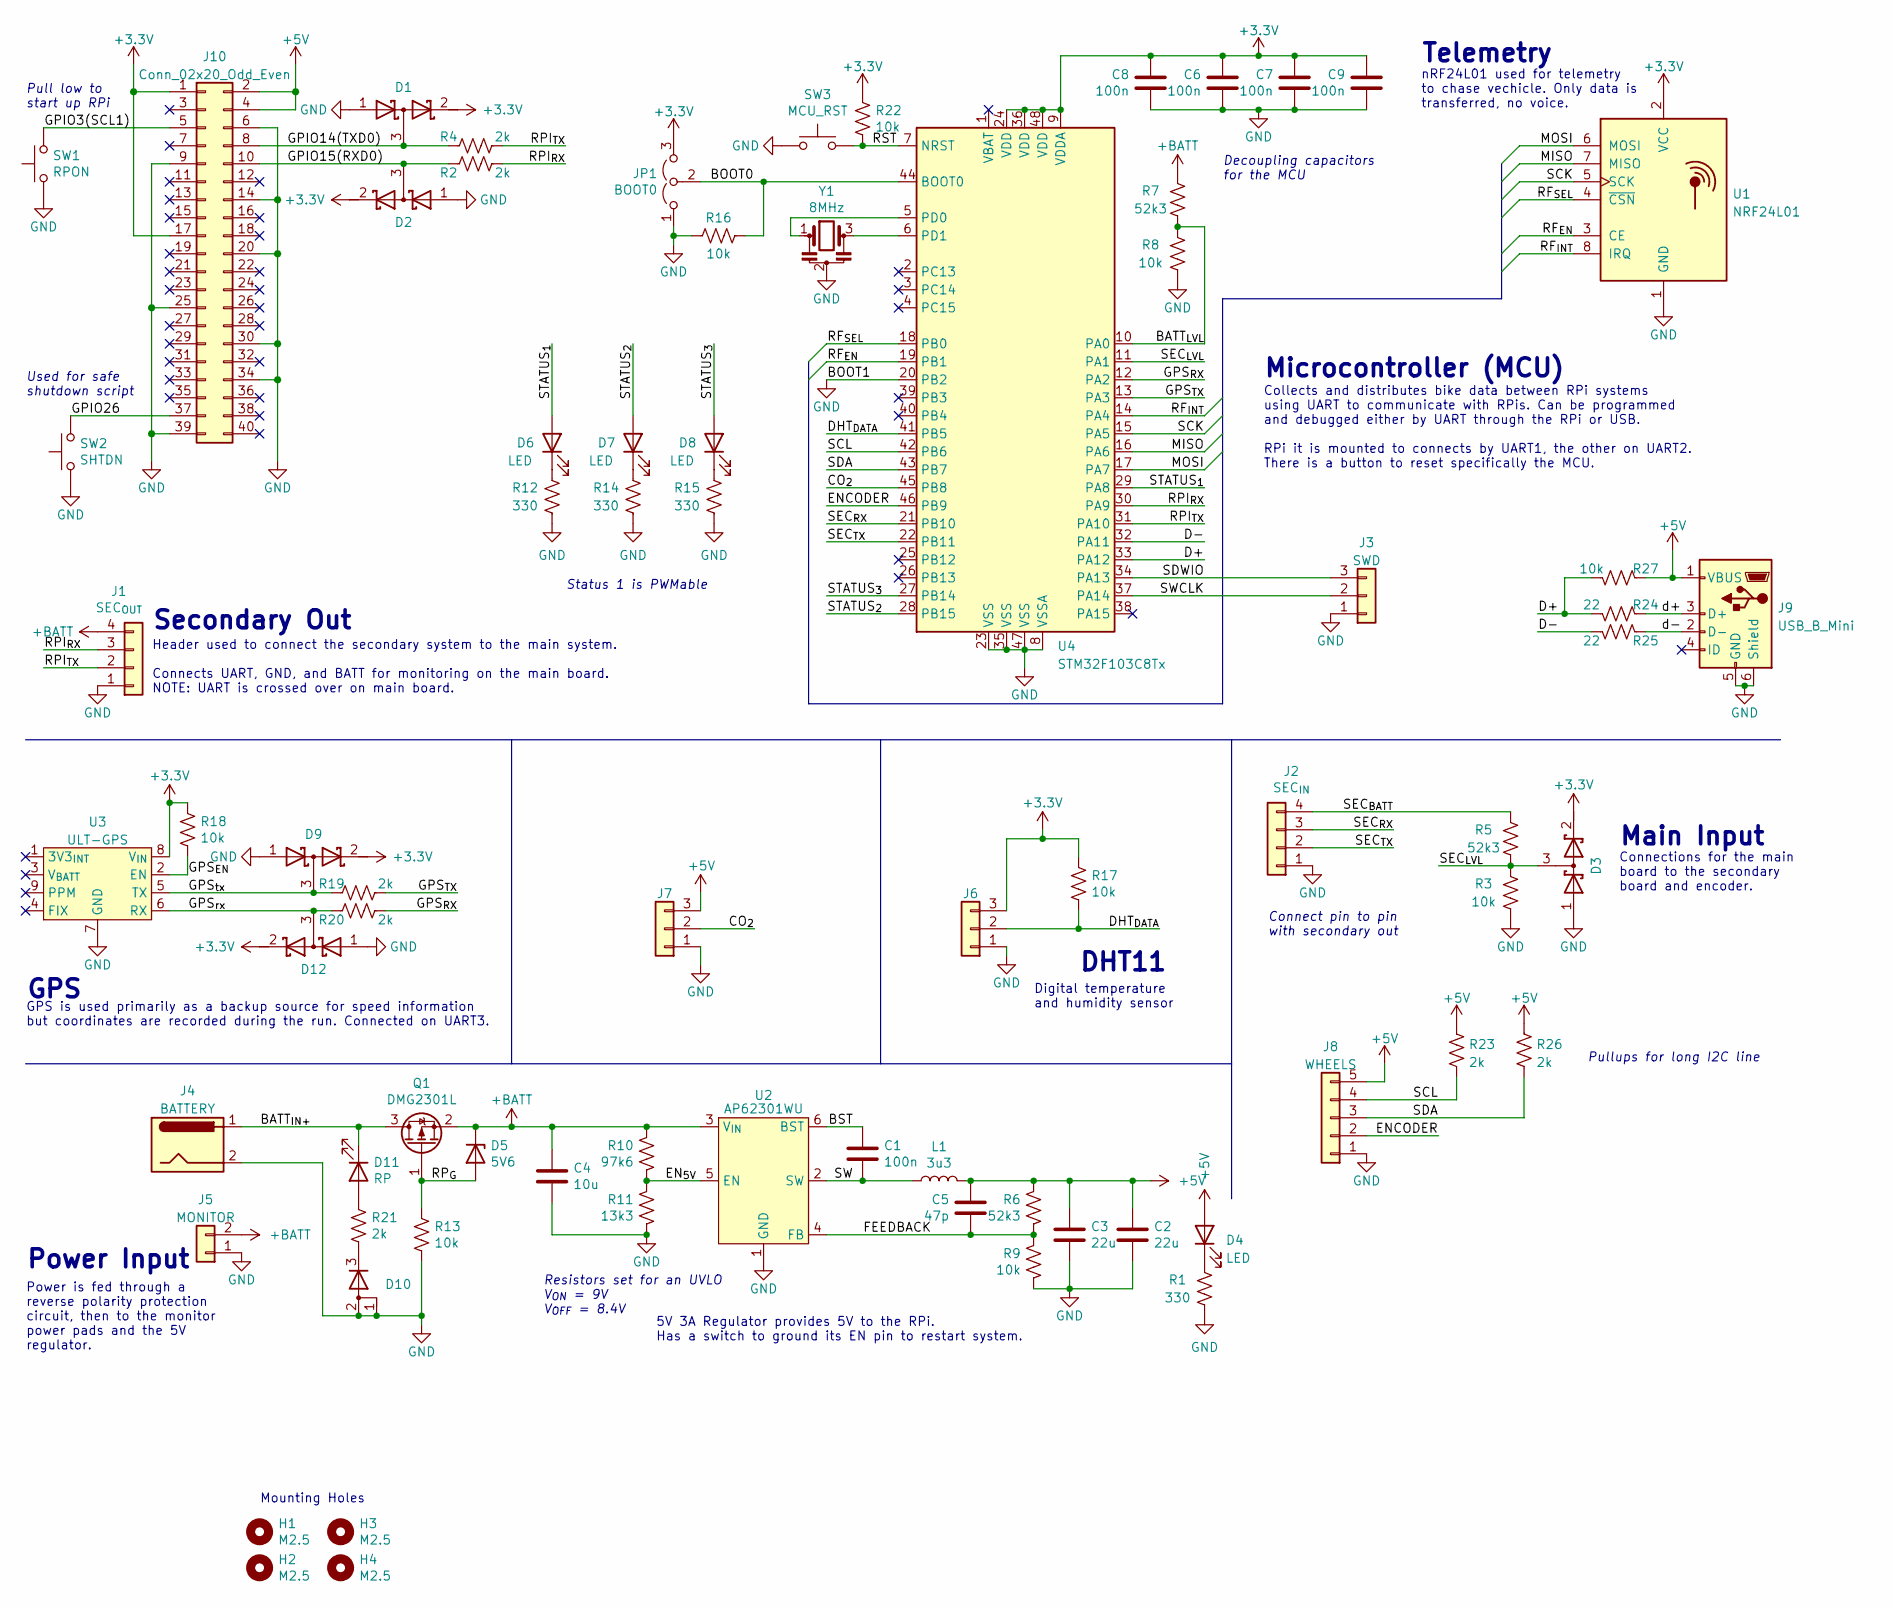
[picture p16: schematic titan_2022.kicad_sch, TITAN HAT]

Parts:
C1, C6, C7, C8, C9: 100n; C_0603_1608Metric
C2, C3: 22u; C_0805_2012Metric
C4: 10u; C_0603_1608Metric
C5: 47p; C_0603_1608Metric
D1, D2, D3, D9, D12: TBAT54S; SOT-23
D4, D6, D7, D8: LED; LED_0805_2012Metric
D5: 5V6; D_SOD-323
D10: BAV70; SOT-23
D11: RP; D_0805_2012Metric
H1, H2, H3, H4: M2.5; MountingHole_2.7mm_M2.5
J1: SEC_{OUT}; Molex_KK-254_AE-6410-04A_1x04_P2.54mm_Vertical
J2: SEC_{IN}; Molex_KK-254_AE-6410-04A_1x04_P2.54mm_Vertical
J3: SWD; PinHeader_1x03_P2.54mm_Vertical
J4: BATTERY; BarrelJack_Wuerth_6941xx301002
J5: MONITOR; SolderWire-1.5sqmm_1x02_P6mm_D1.7mm_OD3mm
J6: DHT; PinHeader_1x03_P2.54mm_Vertical
J7: CO_{2}; PinHeader_1x03_P2.54mm_Vertical
J8: WHEELS; PinHeader_1x05_P2.54mm_Vertical
J9: USB_B_Mini; TE_2172034-1
J10: Conn_02x20_Odd_Even; PinSocket_2x20_P2.54mm_Vertical
JP1: BOOT0; PinHeader_1x03_P2.54mm_Vertical
L1: 3u3; L_Taiyo-Yuden_NR-50xx
Q1: DMG2301L; SOT-23
R1, R12, R14, R15: 330; R_0603_1608Metric
R2, R4, R19, R20, R21, R23, R26: 2k; R_0603_1608Metric
R3, R8, R9, R13, R16, R17, R18, R22, R27: 10k; R_0603_1608Metric
R5, R6, R7: 52k3; R_0603_1608Metric
R10: 97k6; R_0603_1608Metric
R11: 13k3; R_0603_1608Metric
R24, R25: 22; R_0603_1608Metric
SW1: RPON; SW_PUSH_6mm_H4.3mm
SW2: SHTDN; SW_PUSH_6mm_H4.3mm
SW3: MCU_RST; SW_PUSH_6mm_H4.3mm
U1: NRF24L01; nRF24L01_Breakout
U2: AP62301WU; TSOT-23-6
U3: ULT-GPS
U4: STM32F103C8Tx; LQFP-48_7x7mm_P0.5mm
Y1: 8MHz; Resonator_SMD_Murata_CSTxExxV-3Pin_3.0x1.1mm

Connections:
+3V3: C6.2, C7.2, C8.2, C9.2, D1.2 (K), D2.2 (K), D3.2 (K), D9.2 (K), D12.2 (K), J6.3, J10.1, J10.17, JP1.3 (B), R17.2, R18.2, R22.2, U1.2 (VCC), U3.8 (V_{IN}), U4.9 (VDDA), U4.24 (VDD), U4.36 (VDD), U4.48 (VDD)
+5V: C2.1, C3.1, C5.2, D4.2 (A), J7.3, J8.5, J9.1 (VBUS), J10.2, J10.4, L1.2, R6.2, R23.1, R26.1, R27.2
+BATT: C4.2, D5.1 (K), J1.4, J5.2, Q1.2 (S), R7.2, R10.2, U2.3 (V_{IN})
/BATT_{IN+}: D11.1 (K), J4.1, Q1.3 (D)
/BATT_{LVL}: R7.1, R8.2, U4.10 (PA0)
/BOOT0: JP1.2 (C), R16.2, U4.44 (BOOT0)
/BST: C1.2, U2.6 (BST)
/CO_{2}: J7.2, U4.45 (PB8)
/D+: R24.1, R27.1, U4.33 (PA12)
/D-: R25.1, U4.32 (PA11)
/DHT_{DATA}: J6.2, R17.1, U4.41 (PB5)
/ENCODER: J8.2, U4.46 (PB9)
/EN_{5V}: R10.1, R11.2, U2.5 (EN)
/FEEDBACK: C5.1, R6.1, R9.2, U2.4 (FB)
/GPIO3(SCL1): J10.5, SW1.2
/GPIO14(TXD0): D1.3 (common), J10.8, R4.2
/GPIO15(RXD0): D2.3 (common), J10.10, R2.2
/GPIO26: J10.37, SW2.2
/GPS_{EN}: R18.1, U3.2 (EN)
/GPS_{RX}: R20.1, U4.12 (PA2)
/GPS_{TX}: R19.1, U4.13 (PA3)
/GPS_{rx}: D12.3 (common), R20.2, U3.6 (RX)
/GPS_{tx}: D9.3 (common), R19.2, U3.5 (TX)
/MISO: U1.7 (MISO), U4.16 (PA6)
/MOSI: U1.6 (MOSI), U4.17 (PA7)
/RF_{EN}: U1.3 (CE), U4.19 (PB1)
/RF_{INT}: U1.8 (IRQ), U4.14 (PA4)
/RF_{SEL}: U1.4 (~CSN), U4.18 (PB0)
/RPI_{RX}: J1.3, R2.1, U4.30 (PA9)
/RPI_{TX}: J1.2, R4.1, U4.31 (PA10)
/RP_{G}: D5.2 (A), Q1.1 (G), R13.2
/RST: R22.1, SW3.2, U4.7 (NRST)
/SCK: U1.5 (SCK), U4.15 (PA5)
/SCL: J8.4, R23.2, U4.42 (PB6)
/SDA: J8.3, R26.2, U4.43 (PB7)
/SDWIO: J3.3, U4.34 (PA13)
/SEC_{BATT}: J2.4, R5.2
/SEC_{LVL}: D3.3 (common), R3.2, R5.1, U4.11 (PA1)
/SEC_{RX}: J2.3, U4.21 (PB10)
/SEC_{TX}: J2.2, U4.22 (PB11)
/STATUS_{1}: D6.2 (A), U4.29 (PA8)
/STATUS_{2}: D7.2 (A), U4.28 (PB15)
/STATUS_{3}: D8.2 (A), U4.27 (PB14)
/SW: C1.1, L1.1, U2.2 (SW)
/SWCLK: J3.2, U4.37 (PA14)
/d+: J9.3 (D+), R24.2
/d-: J9.2 (D-), R25.2
GND: C2.2, C3.2, C4.1, C6.1, C7.1, C8.1, C9.1, D1.1 (A), D2.1 (A), D3.1 (A), D9.1 (A), D10.1 (A), D10.2 (A), D12.1 (A), J1.1, J2.1, J3.1, J4.2, J5.1, J6.1, J7.1, J8.1, J9.5 (GND), J9.6 (Shield), J10.6, J10.9, J10.14, J10.20, J10.25, J10.30, J10.34, J10.39, JP1.1 (A), R1.1, R3.1, R8.1, R9.1, R11.1, R12.1, R13.1, R14.1, R15.1, R16.1, SW1.1, SW2.1, SW3.1, U1.1 (GND), U2.1 (GND), U3.7 (GND), U4.8 (VSSA), U4.20 (PB2), U4.23 (VSS), U4.35 (VSS), U4.47 (VSS), Y1.2
unnamed: D4.1 (K), R1.2
unnamed: D6.1 (K), R12.2
unnamed: D7.1 (K), R14.2
unnamed: D8.1 (K), R15.2
unnamed: D10.3 (K), R21.1
unnamed: D11.2 (A), R21.2
unnamed: U4.5 (PD0), Y1.1
unnamed: U4.6 (PD1), Y1.3

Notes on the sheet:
Power is fed through a reverse polarity protection circuit, then to the monitor power pads and the 5V regulator.
Microcontroller (MCU)
Connections for the main board to the secondary board and encoder.
GPS
Connect pin to pin with secondary out
Status 1 is PWMable
nRF24L01 used for telemetry to chase vechicle. Only data is transferred, no voice.
Decoupling capacitors for the MCU
Power Input
Collects and distributes bike data between RPi systems using UART to communicate with RPis. Can be programmed and debugged either by UART through the RPi or USB. RPi it is mounted to connects by UART1, the other on UART2. There is a button to reset specifically the MCU.
Header used to connect the secondary system to the main system. Connects UART, GND, and BATT for monitoring on the main board. NOTE: UART is crossed over on main board.
Secondary Out
Mounting Holes
Pullups for long I2C line
Digital temperature and humidity sensor
GPS is used primarily as a backup source for speed information but coordinates are recorded during the run. Connected on UART3.
Pull low to start up RPi
Used for safe shutdown script
5V 3A Regulator provides 5V to the RPi. Has a switch to ground its EN pin to restart system.
DHT11
Resistors set for an UVLO V_{ON} = 9V V_{OFF} = 8.4V
Main Input
Telemetry

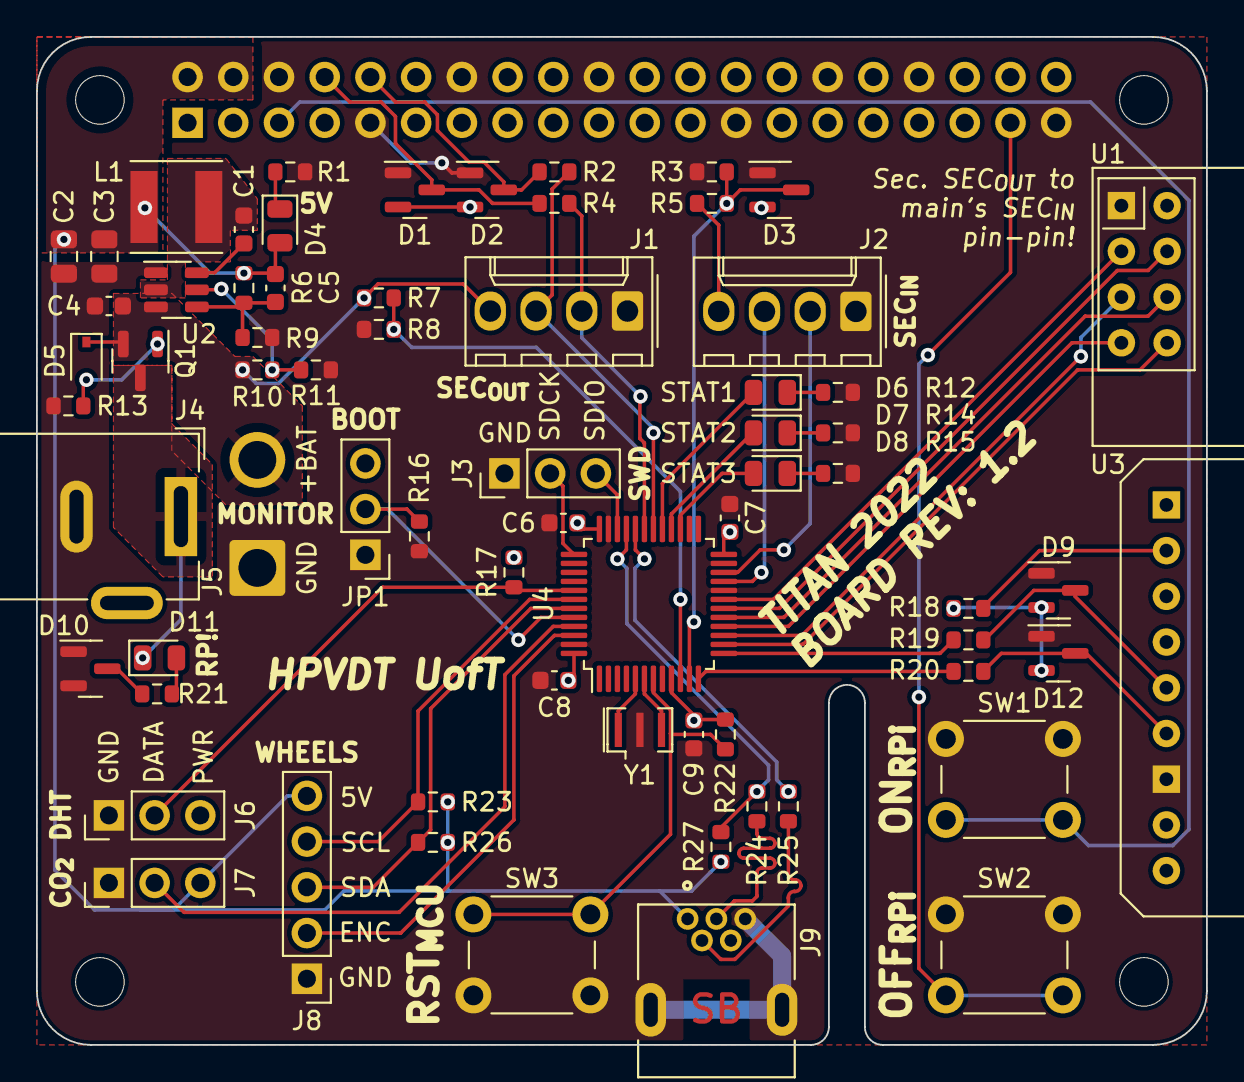
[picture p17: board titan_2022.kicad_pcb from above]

Board: 2 copper layers, 65.0 x 56.0 mm, 73 parts (1 on the bottom side), 56 nets.

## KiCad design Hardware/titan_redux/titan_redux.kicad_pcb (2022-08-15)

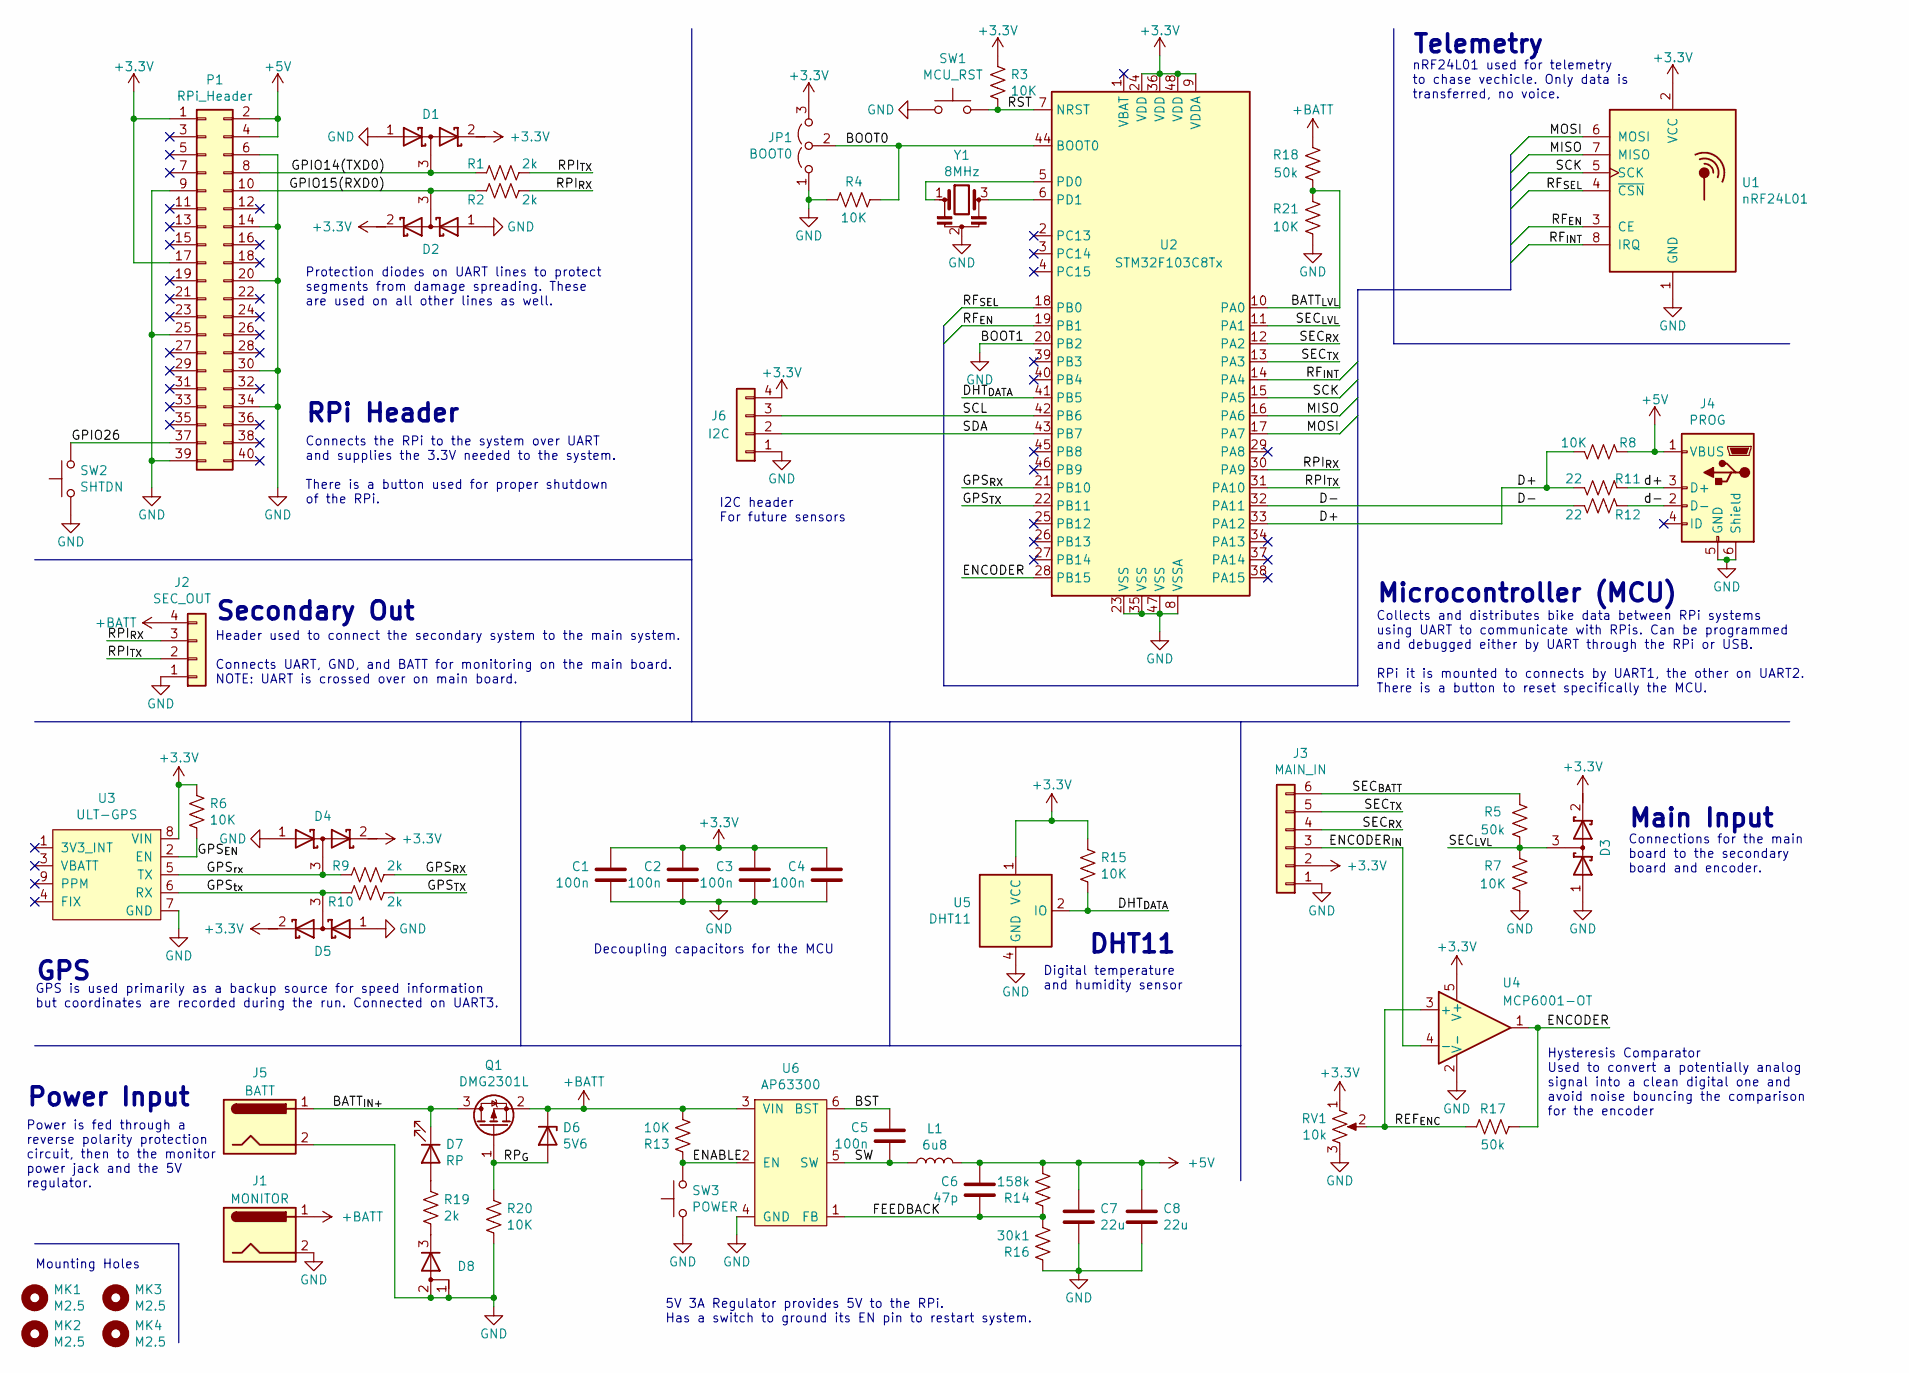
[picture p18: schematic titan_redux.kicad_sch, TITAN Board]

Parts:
C1, C2, C3, C4, C5: 100n; C_0603_1608Metric
C6: 47p; C_0603_1608Metric
C7, C8: 22u; C_0603_1608Metric
D1, D2, D3, D4, D5: TBAT54S; SOT-23
D6: 5V6; D_SOD-323
D7: RP; D_0805_2012Metric
D8: TCMBD914; SOT-23
J1: MONITOR; BarrelJack_Wuerth_6941xx301002
J2: SEC_OUT; PinHeader_1x04_P2.54mm_Vertical
J3: MAIN_IN; PinHeader_1x06_P2.54mm_Vertical
J4: PROG; TE_2172034-1
J5: BATT; BarrelJack_Wuerth_6941xx301002
J6: I2C; PinHeader_1x04_P2.54mm_Vertical
JP1: BOOT0; PinHeader_1x03_P2.54mm_Vertical
L1: 6u8; L_Bourns_SRN6045TA
MK1, MK2, MK3, MK4: M2.5; MountingHole_2.7mm_M2.5
P1: RPi_Header; PinSocket_2x20_P2.54mm_Vertical
Q1: DMG2301L; SOT-23
R1, R2, R9, R10, R19: 2k; R_0603_1608Metric
R3, R4, R6, R7, R8, R13, R15, R20, R21: 10K; R_0603_1608Metric
R5, R17, R18: 50k; R_0603_1608Metric
R11, R12: 22; R_0603_1608Metric
R14: 158k; R_0603_1608Metric
R16: 30k1; R_0603_1608Metric
RV1: 10k; Potentiometer_Bourns_3296W_Vertical
SW1: MCU_RST; SW_PUSH_6mm_H4.3mm
SW2: SHTDN; SW_PUSH_6mm_H4.3mm
SW3: POWER; SW_PUSH_6mm_H4.3mm
U1: nRF24L01; nRF24L01_Breakout
U2: STM32F103C8Tx; LQFP-48_7x7mm_P0.5mm
U3: ULT-GPS
U4: MCP6001-OT; SOT-23-5
U5: DHT11; Aosong_DHT11_5.5x12.0_P2.54mm
U6: AP63300; TSOT-23-6
Y1: 8MHz; Resonator_SMD_muRata_CSTxExxV-3Pin_3.0x1.1mm

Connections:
+3V3: C1.2, C2.2, C3.2, C4.2, D1.2 (K), D2.2 (K), D3.2 (K), D4.2 (K), D5.2 (K), J3.2, J6.4, JP1.3 (B), P1.1, P1.17, R3.2, R6.2, R15.2, RV1.1, U1.2 (VCC), U2.9 (VDDA), U2.24 (VDD), U2.36 (VDD), U2.48 (VDD), U3.8 (VIN), U4.5 (V+), U5.1 (VCC)
+5V: C6.2, C7.1, C8.1, J4.1 (VBUS), L1.2, P1.2, P1.4, R8.2, R14.1
+BATT: D6.1 (K), J1.1, J2.4, Q1.2 (S), R13.1, R18.2, U6.3 (VIN)
/BATT_{IN+}: D7.1 (K), J5.1, Q1.3 (D)
/BATT_{LVL}: R18.1, R21.2, U2.10 (PA0)
/BOOT0: JP1.2 (C), R4.2, U2.44 (BOOT0)
/BST: C5.2, U6.6 (BST)
/D+: R8.1, R11.1, U2.33 (PA12)
/D-: R12.1, U2.32 (PA11)
/DHT_{DATA}: R15.1, U2.41 (PB5), U5.2 (IO)
/ENABLE: R13.2, SW3.2, U6.2 (EN)
/ENCODER: R17.2, U2.28 (PB15), U4.1
/ENCODER_{IN}: J3.3, U4.4 (-)
/FEEDBACK: C6.1, R14.2, R16.1, U6.1 (FB)
/GPIO14(TXD0): D1.3 (common), P1.8, R1.2
/GPIO15(RXD0): D2.3 (common), P1.10, R2.2
/GPIO26: P1.37, SW2.2
/GPS_{EN}: R6.1, U3.2 (EN)
/GPS_{RX}: R9.1, U2.21 (PB10)
/GPS_{TX}: R10.1, U2.22 (PB11)
/GPS_{rx}: D4.3 (common), R9.2, U3.5 (TX)
/GPS_{tx}: D5.3 (common), R10.2, U3.6 (RX)
/MISO: U1.7 (MISO), U2.16 (PA6)
/MOSI: U1.6 (MOSI), U2.17 (PA7)
/REF_{ENC}: R17.1, RV1.2, U4.3 (+)
/RF_{EN}: U1.3 (CE), U2.19 (PB1)
/RF_{INT}: U1.8 (IRQ), U2.14 (PA4)
/RF_{SEL}: U1.4 (~CSN), U2.18 (PB0)
/RPI_{RX}: J2.3, R2.1, U2.30 (PA9)
/RPI_{TX}: J2.2, R1.1, U2.31 (PA10)
/RP_{G}: D6.2 (A), Q1.1 (G), R20.2
/RST: R3.1, SW1.2, U2.7 (NRST)
/SCK: U1.5 (SCK), U2.15 (PA5)
/SCL: J6.3, U2.42 (PB6)
/SDA: J6.2, U2.43 (PB7)
/SEC_{BATT}: J3.6, R5.2
/SEC_{LVL}: D3.3 (common), R5.1, R7.2, U2.11 (PA1)
/SEC_{RX}: J3.4, U2.12 (PA2)
/SEC_{TX}: J3.5, U2.13 (PA3)
/SW: C5.1, L1.1, U6.5 (SW)
/d+: J4.3 (D+), R11.2
/d-: J4.2 (D-), R12.2
GND: C1.1, C2.1, C3.1, C4.1, C7.2, C8.2, D1.1 (A), D2.1 (A), D3.1 (A), D4.1 (A), D5.1 (A), D8.1 (A), D8.2 (A), J1.2, J2.1, J3.1, J4.5 (GND), J4.6 (Shield), J5.2, J6.1, JP1.1 (A), P1.6, P1.9, P1.14, P1.20, P1.25, P1.30, P1.34, P1.39, R4.1, R7.1, R16.2, R20.1, R21.1, RV1.3, SW1.1, SW2.1, SW3.1, U1.1 (GND), U2.8 (VSSA), U2.20 (PB2), U2.23 (VSS), U2.35 (VSS), U2.47 (VSS), U3.7 (GND), U4.2 (V-), U5.4 (GND), U6.4 (GND), Y1.2
unnamed: D7.2 (A), R19.2
unnamed: D8.3 (K), R19.1
unnamed: U2.5 (PD0), Y1.1
unnamed: U2.6 (PD1), Y1.3

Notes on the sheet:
5V 3A Regulator provides 5V to the RPi. Has a switch to ground its EN pin to restart system.
Connections for the main board to the secondary board and encoder.
DHT11
Power Input
Telemetry
Main Input
Mounting Holes
GPS is used primarily as a backup source for speed information but coordinates are recorded during the run. Connected on UART3.
nRF24L01 used for telemetry to chase vechicle. Only data is transferred, no voice.
Connects the RPi to the system over UART and supplies the 3.3V needed to the system. There is a button used for proper shutdown of the RPi.
Collects and distributes bike data between RPi systems using UART to communicate with RPis. Can be programmed and debugged either by UART through the RPi or USB. RPi it is mounted to connects by UART1, the other on UART2. There is a button to reset specifically the MCU.
Protection diodes on UART lines to protect segments from damage spreading. These are used on all other lines as well.
GPS
I2C header For future sensors
Digital temperature and humidity sensor
RPi Header
Power is fed through a reverse polarity protection circuit, then to the monitor power jack and the 5V regulator.
Header used to connect the secondary system to the main system. Connects UART, GND, and BATT for monitoring on the main board. NOTE: UART is crossed over on main board.
Decoupling capacitors for the MCU
Hysteresis Comparator Used to convert a potentially analog signal into a clean digital one and avoid noise bouncing the comparison for the encoder
Secondary Out
Microcontroller (MCU)

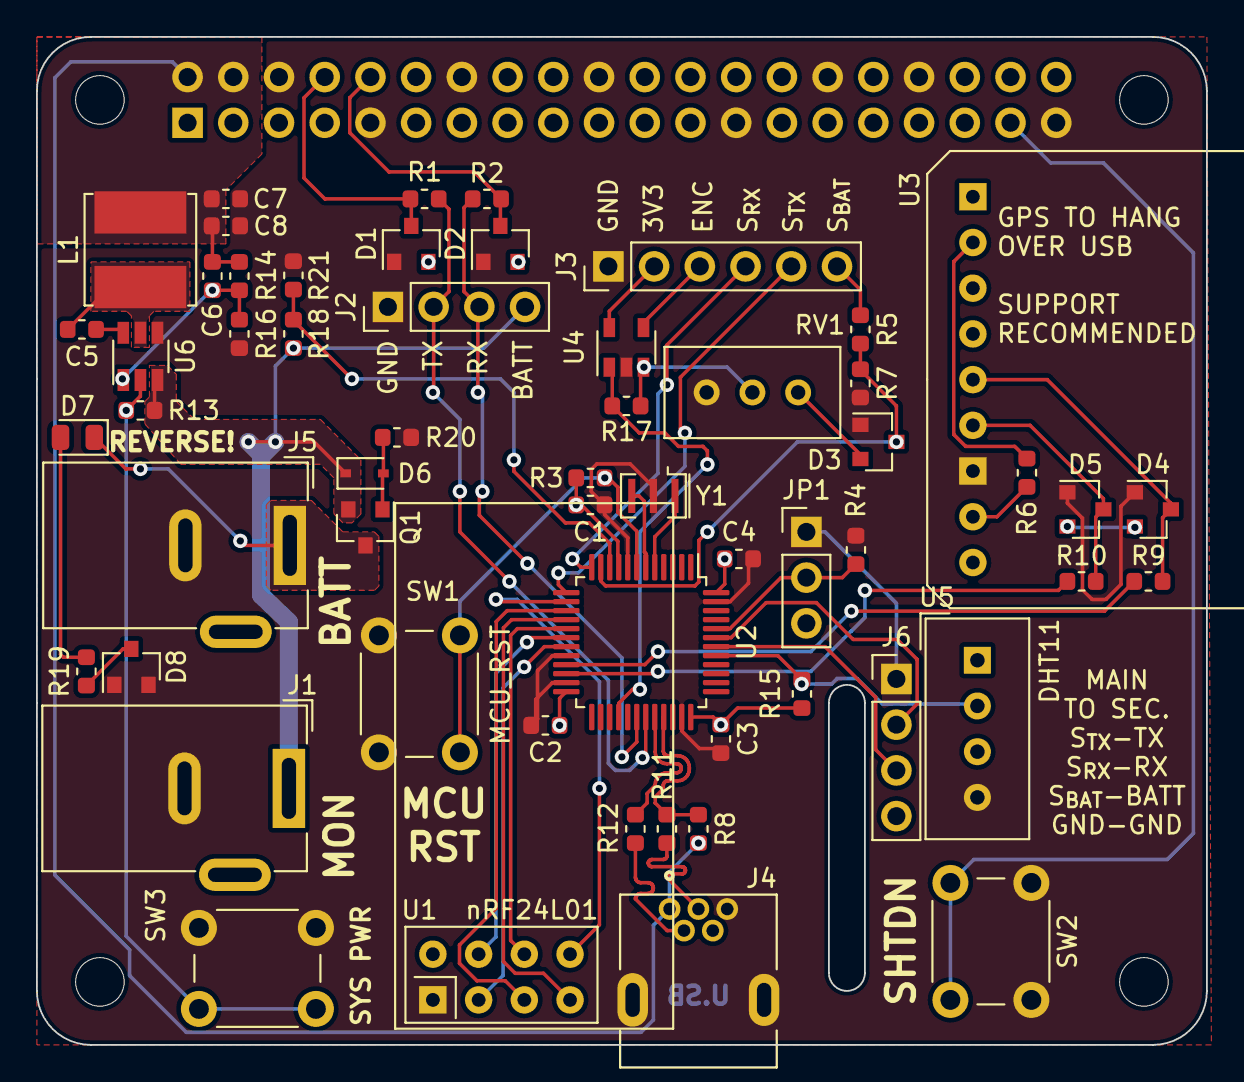
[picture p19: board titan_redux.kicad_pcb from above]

Board: 2 copper layers, 65.0 x 56.0 mm, 62 parts (1 on the bottom side), 47 nets.

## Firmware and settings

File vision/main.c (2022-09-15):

#include "main.h"
#define powerAvgFrames 50 // Needs to be #define for array sizes

int numberFrames = -1; // Number of frames to render for testing (-1 for infinite)
const float CIRCUMFERENCE = 2.104;

// Serial configuration
bool useSerial = false; // Use serial or not
int serialLine = -1;

bool collectANT = false; 	   // Use ANT data from USB?
bool enableLogging = false;   // Logging configuration
bool enableCamera = false;    // Camera
bool isFront = true;          // Is front or not

int main(int argc, char *argv[]) {
   printf(ANSI_COLOUR_BLUE "\n==================\n! TITAN 2022 HUD !\n==================" ANSI_COLOUR_RESET);
   
   // Start by reading in arguements
   printf("\n\nExpected arguements when called in order: 'setup string' 'number of frames'\n");
   printf("\tSpecify role with 'f' or 'r' (assumed to be front if not specified)\
         \n\tEnable camera with 'c'\n\tEnable logging with 'l'\
         \n\tEnable ANT collection with 'a'\n\tEnable serial coms with 's'\
         \n\n\tFrames as -1 for infinty, otherwise the number wanted.\
         \n\tE.g. 'bike.bin fc 10' sets system for front operation with camera for 10 frames\n");
   
   // Read in configuration using a run through switch based on arguement count
   // Note: arguement 0 is the call to run the program itself e.g. "./bike.bin"
   int characterToRead = 0;
   switch (argc) {
      case 3:
         // Get frame count
         numberFrames = atoi(argv[2]);
      case 2:
         // Go through setup string
         do {
            switch (argv[1][characterToRead]) {
               case 'l':
                  enableLogging = true;
                  break;
               case 's':
                  useSerial = true;
                  break;
               case 'a':
                  collectANT = true;
                  break;
               case 'c':
                  enableCamera = true;
                  break;
               case 'r':
                  isFront = false;
                  break;
               case 'f':
                  isFront = true;
                  break;
            }
         } while (argv[1][characterToRead++] != '\0'); 
         break;
   }
   

   
   // Reguritate configuration
   printf("\nParsed configuration:\n" ANSI_COLOUR_YELLOW);
   if (isFront == true) printf("\tRole: FRONT\n");
   else printf("\tRole: REAR\n");
   printf("\tCamera running: %d\n", enableCamera);
   printf("\tCollecting ANT data: %d\n", collectANT);
   printf("\tCommunicate over serial: %d\n", useSerial);
   printf("\tLogging: %d\n", enableLogging);
   if (numberFrames > 0) printf("\tNumber of frames: %d\n\n" ANSI_COLOUR_RESET, numberFrames);
   else printf("\tNo limit to number of frames.\n\n" ANSI_COLOUR_RESET);
   
   // Local variables
   int frontCadence = 0, rearCadence = 0; 
   int frontPower = 0, rearPower = 0;
   int frontHeartRate = 0, rearHeartRate = 0;
   int ANTData[] = {0,0,0,0,0,0};
   int rearBattery = 0, frontBattery = 0;
   int rotations = 0;
   float speedWheel = 0.0;
   float distanceWheel = 0.0, distanceGPS = 0.0;
   float temperature = 0.0;
   float humidity = 0.0;
   float performanceFactor = 0.0;
   float frontBrakeTemp = 200.0, rearBrakeTemp = 200.0;
   int ppmCO2 = 0;
   float speedGPS = 0.0;
   
   // Open serial line
   if (useSerial == true) {
      serialLine = openLine("/dev/serial0");
      
      if (serialLine != -1) printf(ANSI_COLOUR_GREEN "Successfully opened serial line!\n" ANSI_COLOUR_RESET);
      else {
         printf(ANSI_COLOUR_RED "FAILED TO OPEN SERIAL LINE!\nReverting to non-serial behavior.\n" ANSI_COLOUR_RESET);
         useSerial = false;
      }
   }
   else printf(ANSI_COLOUR_RED "NOT USING SERIAL DATA.\n" ANSI_COLOUR_RESET);
   
   // Inform if ANT data is expected, and set up stdin accordingly
   if (collectANT == true) {
      printf("Expecting ANT data to be piped in.\n");
      fcntl(0, F_SETFL, O_NONBLOCK); // Set stdin (0) to be non-blocking
   }
   else if (useSerial == true) printf(ANSI_COLOUR_GREEN "Not collecting ANT data locally, requesting ANT data over serial.\n" ANSI_COLOUR_RESET);
   else printf(ANSI_COLOUR_RED "NOT USING ANY ANT DATA. DISPLAYING RANDOM ANT DATA!\n" ANSI_COLOUR_RESET);
   
   // Start RaceSim
   setupRaceSim();
   
   // Start logging
   if (enableLogging == true) startLogging();
   else printf(ANSI_COLOUR_YELLOW "NOT LOGGING DATA!\n" ANSI_COLOUR_RESET);
   
   // Print camera status
   if (enableCamera == true) printf(ANSI_COLOUR_RESET "Camera will be launched shortly!\n" ANSI_COLOUR_RESET);
   else printf(ANSI_COLOUR_RED "Camera not configured to start.\n" ANSI_COLOUR_RESET);
      
   sleep(3); // Pause to show config before potentially running camera
   
   printf("\n=========================================================\n");
   printf("RUNNING MAIN LOOP");
   printf("\n=========================================================\n\n");
   
   
   // Timing the entire process
   struct timespec tSystemStart,tSystemEnd;
   clock_gettime(CLOCK_MONOTONIC, &tSystemStart); // Get start time
   clock_t titanProcessClock = clock(); // Get start processor time
   
   startOverlay(enableCamera);
   
   // Main HUD loop
   int framesRemaining = numberFrames;
   do {
      
      // ANT data
      printf("Grabbing ANT data\n");
      if (collectANT == true) getANTDataPipedIn(ANTData, serialLine);      // It is meant to collect data locally
      else if (useSerial == false) { 
         // Cant' collect nor request ANT data, use random numbers
         ANTData[0] = 60;
         ANTData[1] = 60;
         ANTData[2] = 120;
         ANTData[3] = 60;
         ANTData[4] = 60;
         ANTData[5] = 120;
      }
      
      // Copy to nicer named variables
      frontHeartRate = ANTData[0];
      frontCadence = ANTData[1];
      frontPower = ANTData[2];
      rearHeartRate = ANTData[3];
      rearCadence = ANTData[4];
      rearPower = ANTData[5];

      
      // Get bike data
      if (useSerial == true) { // Collect bike data from STM32 over serial      
         printf("Grabbing serial data\n");
         
         char bulkBuffer[32];
         startTrial(); requestData(serialLine, '{', &bulkBuffer[1]); 
         
         struct bulkDataStruct {
            char messageType;
            char messageLength;
            uint16_t distGPS;
            uint32_t speedEncoder;
            uint32_t speedGPS;
            uint16_t rotations;
            uint16_t frontBrakeT;
            uint16_t rearBrakeT;
            uint8_t fBatt;
            uint8_t rBatt;
            uint8_t humid;
            uint8_t temp;
            uint16_t CO2;
            uint8_t fhr;
            uint8_t rhr;
            uint8_t fcad;
            uint8_t rcad;
            uint16_t fpwr;
            uint16_t rpwr;
         } dataLoad;
         
         memcpy(&dataLoad, bulkBuffer, sizeof(dataLoad));
         dataLoad.messageType = '[';
         
         distanceGPS = dataLoad.distGPS / 1000.0;
         speedWheel = dataLoad.speedEncoder / 1000.0;
         speedGPS = dataLoad.speedGPS / 1000.0;
         rotations = dataLoad.rotations;
         frontBrakeTemp = dataLoad.frontBrakeT / 100.0;
         rearBrakeTemp =dataLoad.rearBrakeT / 100.0;
         frontBattery = dataLoad.fBatt;
         rearBattery = dataLoad.rBatt;
         humidity = dataLoad.humid / 2.0;
         temperature = (dataLoad.temp - 50.0) / 2.0;
         ppmCO2 = dataLoad.CO2;
         frontHeartRate = dataLoad.fhr;
         rearHeartRate = dataLoad.rhr;
         frontCadence = dataLoad.fcad;
         rearCadence = dataLoad.rcad;
         frontPower = dataLoad.fpwr;
         rearPower = dataLoad.rpwr;

         endTrialIgnore("Bulk transfer", 30);

         distanceWheel = rotations * CIRCUMFERENCE / 1000.0;
         
         /*
         printf("Message type: %c, length char %c\n", dataLoad.messageType, dataLoad.messageLength);
         printf("\tSpeeds: %.3f / %.3f\n", speedWheel, speedGPS);
         printf("\tDist: %.3f / %.3f\n", distanceWheel, distanceGPS);
         printf("\tBrake Temps: %.2f / %.2f\n", frontBrakeTemp, rearBrakeTemp);
         printf("\tBatteries: %d / %d\n", frontBattery, rearBattery);
         printf("\tAtmosphere: %.1f degC, %.1f %%RH, %d ppmCO2\n", temperature, humidity, ppmCO2);
         printf("\tANT front: HR %d | CAD %d | PWR %d\n", frontHeartRate, frontCadence, frontPower);
         printf("\tANT rear: HR %d | CAD %d | PWR %d\n", rearHeartRate, rearCadence, rearPower);
         */
         
      }
      else {
         // Placeholder data for when not collecting anything over serial
         rearBattery = 25;
         frontBattery = 25;
         speedWheel = 120.6;
         distanceWheel = 7;
         temperature = 0.0;
         humidity = 0.0;
         performanceFactor = 101.2;
         frontBrakeTemp = 200.0;
         rearBrakeTemp = 200.0;
         ppmCO2 = 1550;
         speedGPS = 120.6;
         distanceGPS = 6.92;
      }
      
      printf("Averaging power\n");
      // Get average power over powerAvgFrames frames 
      // 10 frames/second, power sensor polls 1 times/second 
      // This does a continuous (rolling) average instead of a periodic average
      if (true) {
         static int frontPowerValues[powerAvgFrames], rearPowerValues[powerAvgFrames];
         static int currentPowerFrame = 0;
         
         // Add current power to rolling buffer
         frontPowerValues[currentPowerFrame] = frontPower;
         rearPowerValues[currentPowerFrame] = rearPower;
         
         // Determine average value for each buffer and save it
         long frontPowerTotal = 0;
         long rearPowerTotal = 0;
         
         for (int i = 0; i < powerAvgFrames; i++) {
            frontPowerTotal = frontPowerTotal + frontPowerValues[i];
            rearPowerTotal = rearPowerTotal + rearPowerValues[i];
         }
         
         frontPower = frontPowerTotal / powerAvgFrames;
         rearPower = rearPowerTotal / powerAvgFrames;
         
         // Increment and loop current frame index
         currentPowerFrame++;
         currentPowerFrame = currentPowerFrame % powerAvgFrames;
      }
      else {
         printf("you done screw up on the power loop.");
      }
      
      
      printf("Performance factor\n");
      // Performance factor
      performanceFactor = compareToSimulation(speedWheel, distanceWheel, (frontPower + rearPower));

      
      // Overlays
      printf("Making overlay\n");
      if (isFront == true) { // Front overlay
         startTrial();
         updateOverlayFront(speedWheel, distanceWheel, frontPower, frontCadence, frontHeartRate, performanceFactor, frontBrakeTemp, frontBattery, speedGPS);
         endTrialIgnore("front overlay", 100);
      }
      else { // Rear overlay
         startTrial();
         updateOverlayRear(speedWheel, distanceWheel, rearPower, frontPower, rearCadence, rearHeartRate, frontBrakeTemp, rearBrakeTemp, rearBattery, performanceFactor, ppmCO2, speedGPS);
         endTrialIgnore("rear overlay", 100);
      }
      
      
      // Logging
      if (enableLogging == true) {
         printf("Logging\n");
         updateLog(speedWheel, distanceWheel, frontPower, rearPower, 
                  frontCadence, rearCadence, frontHeartRate, rearHeartRate, 
                  temperature, humidity, frontBattery, rearBattery,
                  frontBrakeTemp, rearBrakeTemp, ppmCO2, performanceFactor,
                  speedGPS, distanceGPS);
      }
      
      // Count down number of frames if there was a limit stated
      if (numberFrames > 0) framesRemaining--;
   } while ((framesRemaining != 0) || (numberFrames == -1));
   
   // Overal time
   titanProcessClock = clock() - titanProcessClock; // Get run time
   clock_gettime(CLOCK_MONOTONIC, &tSystemEnd); // Get end time
   float secondsElapsed = ((float) titanProcessClock)/CLOCKS_PER_SEC;
   
   float overallDelta = (tSystemEnd.tv_sec - tSystemStart.tv_sec) + ((tSystemEnd.tv_nsec - tSystemStart.tv_nsec) / 1000000000.0);
   
   printf(ANSI_COLOUR_MAGENTA "\nIt took %2.3f processor seconds, %.3f realtime seconds for %d frames.\n" ANSI_COLOUR_RESET, secondsElapsed, overallDelta, numberFrames);
   printf(ANSI_COLOUR_MAGENTA "An average of %.3f realtime seconds for each frame (%.2f fps).\n" ANSI_COLOUR_RESET, overallDelta / numberFrames, numberFrames / overallDelta);
   
   closeOverlay();
   
   return 0;
}

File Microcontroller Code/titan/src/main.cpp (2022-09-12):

#include <Arduino.h>
#include "communication.h"
#include "sensors.h"
#include "led.h"

void setup() {
  setupLEDs();
  setupCommunication(); // Must be first for potential begging
  setupSensors();
  ledOn(2); // Turn on LED 2 for all operation
}

void loop() {
  if (frontSerial.available()) {
    // Data on front line
    processData('f');
  }
  if (rearSerial.available()) {
    // Data on rear line
    processData('r');
  }
#ifdef ALLOW_DEBUG_SERIAL
  if (DEBUGSERIAL.available()) {
    // Data on debugging line
    processData('d');
  }
#endif

  // Telemetry Check
  if(recievedRadioData) {
    radioRecieved();
    recievedRadioData = false;
    processData('t');
  }

  // Periodic checks of different sensors
  // Their update conditions/periods are set in their files
  checkHDT();
  checkBrakeTemps();
  checkBatteries();
  checkEncoderTimeout();
  GPSCheck();

  heartBeat(); // Used to visualize load
  delayMicroseconds(500); // Regular delay
}

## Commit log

2019-11-03 Arduino code
    Initial commit
2019-11-03 Python Code
    [WHPSC.csv]
2019-11-03 Modified Python ANT+ Library
    [buildout.cfg]
2019-11-04 Repiping errors
    - Changed OSD to use 'update' instead of layer swapping
    - Added code to output errors to a null device for the duration of 'update' to allow it to be run in terminal.
    - Cycle time cut down to ~70ms!
2021-06-07 Added harware design files
    [1604A430_LEVER-LOCK HINGE.SLDPRT, Disc Caliper Mount, Rear.SLDPRT, Display PCB mount assembly.SLDASM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]
2022-07-21 Delete TitanVisionFirmwarePython directory
    Not needed, moving to C-based OSD system
    [WHPSC.csv, buildout.cfg]
2022-07-21 Upload of C based OSD
    OSD based on writing directly to the video driver
2022-07-22 Added code to start and stop camera preview
2022-07-23 Updated Serial object definition
    Updated Serial object declaration to be in line with new STM32 core
    https://github.com/stm32duino/wiki/wiki/API#hardwareserial
2022-07-23 Removed LED code
2022-07-24 Made python script ignore temporary pipe issues
    [titanant.py]
2022-07-24 Matching STM32 specified baudrate
2022-07-24 Added system to disable camera for tests
2022-08-03 Added Arduino based telemetry station code
2022-08-04 Removed irrelevant encoder test code
2022-08-04 Added hardware timer test code
2022-08-04 Removed useless SPI related code
2022-08-15 Removing hardware files from 2019
    [1604A430_LEVER-LOCK HINGE.SLDPRT, Disc Caliper Mount, Rear.SLDPRT, Display PCB mount assembly.SLDASM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]
2022-08-15 Upload of my 2020 redux hardware
    [2172034-1--3DModel-STEP-56544.STEP, CUI_DEVICES_PJ-002B.step, titan_redux.kicad_pcb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]
2022-08-15 Uploaded TITAN 2022 electronics system as ordered
    [2172034-1--3DModel-STEP-56544.STEP, DC Power Jack 5.5mm x 2.1mm.STEP, TCRT5000.step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]
2022-08-16 Cleaned up schematics
    [titan_2022.kicad_sch, titan_wheel.kicad_pcb, titan_wheel.kicad_sch]
2022-08-17 Added scripts to start system and safely power down
2022-08-18 Fixing arguement parsing indexes
    [main.c]
2022-08-19 Added brake temperature
2022-08-19 Added CO2 sensor support
2022-08-19 Disabled radio prints
2022-08-19 Moved brake code to seperate files
2022-08-19 Added LED library
2022-08-19 Added hardware timer based encoder
2022-08-23 Fixed note for wheel LED
    [titan_wheel.kicad_sch]
2022-08-23 Added build option for clone STM32s
2022-08-23 Added checks for if a brake is missing or not
2022-08-23 Fixed heartbeat and added LED flashes in setup
2022-08-28 Fixed reading for rear brake temperature
2022-08-30 Calibrated battery voltage division
2022-09-01 Added colour to C code print statements
2022-09-01 Fixed original encoder code
2022-09-01 Tweaked battery system based on tests
2022-09-01 Hardcoded emissivity for brake disks
2022-09-06 Add GPS spd to display. Change power to avg power.
2022-09-07 modified files to work on raspberry pi
2022-09-07 Added ledSet and comments
2022-09-07 Added polling for CO2 sensor
2022-09-07 Interrupt based CO2 sensor monitoring
2022-09-07 Added blinking to brakes for error pick up
2022-09-07 Added passthrough code for TITAN redux board
2022-09-12 Removed obsolete and outdated Arduino sketch for TITAN
2022-09-12 Added error LEDs to setups
    [main.cpp]
2022-09-12 Set default radio power to maximum
2022-09-13 Changed name for encoder speed
2022-09-15 Fixed power averaging issue
    [main.c]
2022-09-15 Fixed return to desktop script
    [go_to_desktop.py]
2022-09-15 Changed periodic power averaging to continuous averaging
2022-12-31 Raised radio power to MAX
    Explains the short range of TITAN at WHPSC 2022. This should be tested for stability due to power draw, low if needed.
